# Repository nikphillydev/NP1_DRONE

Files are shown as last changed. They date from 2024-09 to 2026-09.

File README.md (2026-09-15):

# NP1 DRONE
I am attempting to build a quadcopter from scratch, both the PCB hardware (using KiCAD) and software (C/C++ on STM32).

I am a computer software engineering student at the University of Alberta. I started this project in early 2024 to push myself with embedded systems. Since its inception, I have learned a ton about PCB design and FreeRTOS firmware on STM32 microcontrollers. 

Everything I make in this project is from scratch. The STM32-based circuit boards are designed with KiCAD and ordered from JLCPCB with assembly. I am using FreeRTOS for the software because of its scalability in complex embedded projects. I have written all the device drivers from scratch, and wholly designed the multi-threaded architecture for each of the drone's sub-systems.

Each sub-system presents its own set of challenges. As an overview, there are 3 sub-systems of the NP1 Drone:
```
                     (Over-The-Air Messaging)                               (CANBUS)
[RC CONTROLLER]   <---------------------------->  [Flight Controller]   <--------------->  [Electronic Speed Controller] x4
```
#### 1. Flight Controller Overview
The Flight Controller (FCC) is a custom PCB design whose software runs the control system for the drone. In order to achieve this, it must 1) receive pilot input from the RC Controller, and 2) estimate its attitude and heading (roll, pitch, yaw). These inputs enter the onboard PID controller in order to calculate the necessary motor commands to send to the Electronic Speed Controllers (ESCs).

The FCC is equipped with a multitude of sensors, namely an IMU, magnetometer, barometer, optical flow sensor, and range finder. It performs sensor fusion through the use of an Extended Kalman Filter (EKF) and a few other custom algorithms. When it receives Over-The-Air (OTA) messages from the RC Controller, it monitors for a HEARTBEAT signal to detect LOSS-OF-LINK and perform flight termination. The control system interprets pilot input and sets the target roll, pitch, and yaw accordingly depending on flight mode (various flight modes still WIP).

<p align="center">
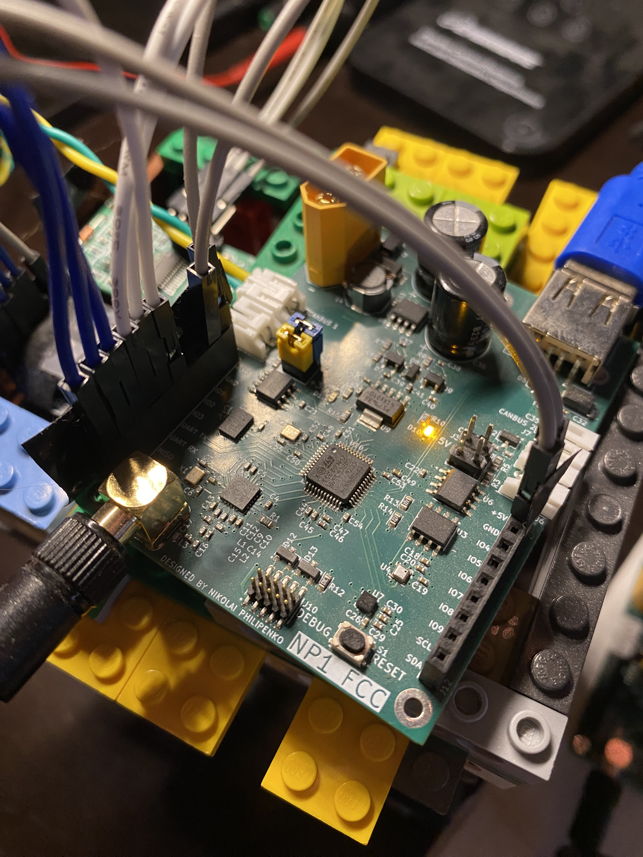
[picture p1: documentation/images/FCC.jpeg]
Flight Controller
  <br>
  <sub><b>Figure 1:</b> The Flight Controller (FCC) sitting on a Lego frame. The USB powers the board and enables logging to my laptop; jumper wires connect the external range finder and optical flow sensor; the green and yellow twisted pair connect to the ESCs using CANBUS.</sub>
</p>

#### 2. RC Controller Overview
The RC Controller is simple: receive pilot input from various joysticks and buttons and send those values Over-The-Air (OTA) to the FCC. A custom OTA messaging protocol (modelled after MAVLINK) has been developed to facilitate this communication. The physical inputs of the RC Controller are fairly WIP right now. Currently, its a breadboard with push-buttons and a potentiometer, (hopefully) soon it will be a PS4 controller.

<p align="center">
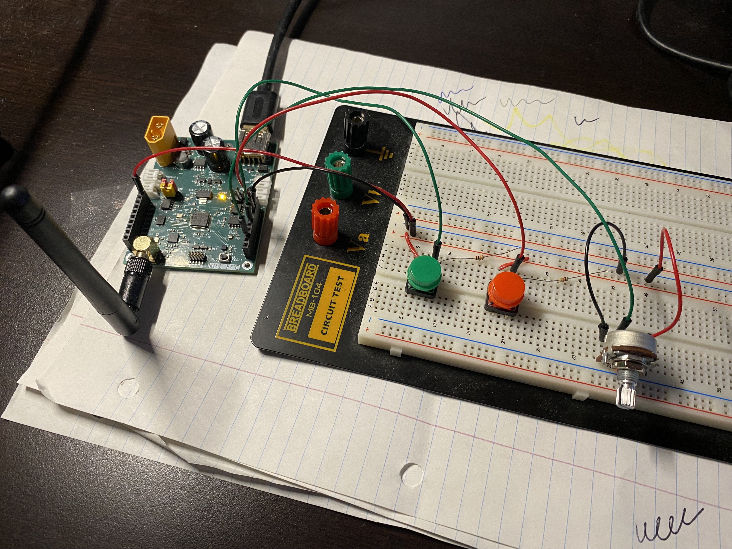
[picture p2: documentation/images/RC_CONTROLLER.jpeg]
RC Controller
  <br>
  <sub><b>Figure 2:</b> The RC Controller, in its current state. Spare hardware is used to capture pilot input.</sub>
</p>

#### 3. Electronic Speed Controller Overview
The Electronic Speed Controller (ESC) requires a strong understanding of Brushless DC (BLDC) motor control. The custom PCB design and software are designed around the (sensorless) 6-Step Trapezoidal control method, where a Back Electromotive Force (BEMF) measurement from the floating motor phase is measured in order to know when to switch the commutation to the next step. In order to perform proper closed-loop control in this method, the motor must be spinning fast enough to generate a sufficient BEMF. I designed the ESC to operate in a software defined state-machine. Here are the states:
1. STAND-BY: ESC is not commanding a rotation of the motor.
2. ARMING: Align-and-Go Step. ESC commands an open-loop ramp up of the motor to obtain sufficient BEMF measurements. Lasts for about 0.8 sec.
3. ARMED: ESC is commanding true closed-loop, 6-Step commutation with BEMF zero-crossing detection.

The ESC receives ARM, DISARM, and THROTTLE CANBUS messages from the FCC to transition between its internal states and increase / decrease motor RPM.

<table align="center">
  <tr>
    <td align="center" valign="top">
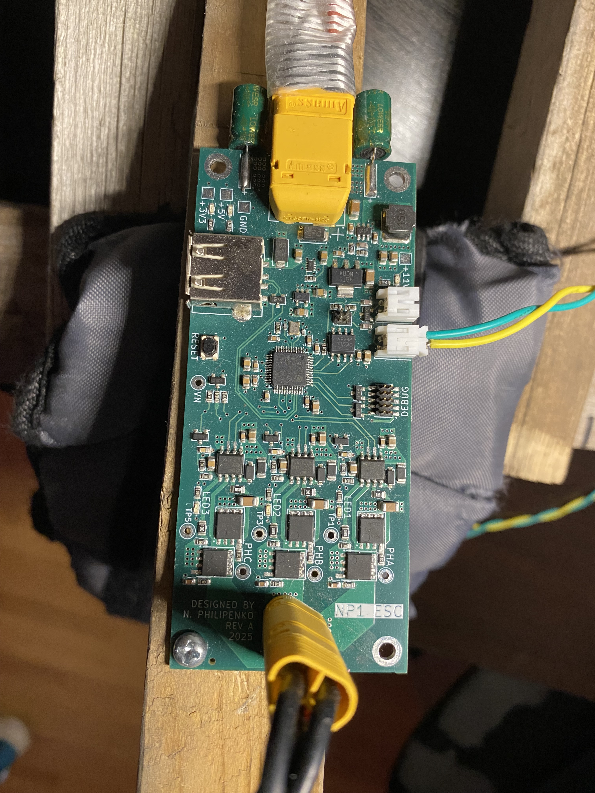
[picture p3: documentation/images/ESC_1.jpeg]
Electronic Speed Controller
      <br>
      <sub><b>Figure 2:</b> The Electronic Speed Controller (ESC), connected to the FCC via CANBUS.</sub>
    </td>
    <td align="center" valign="top">
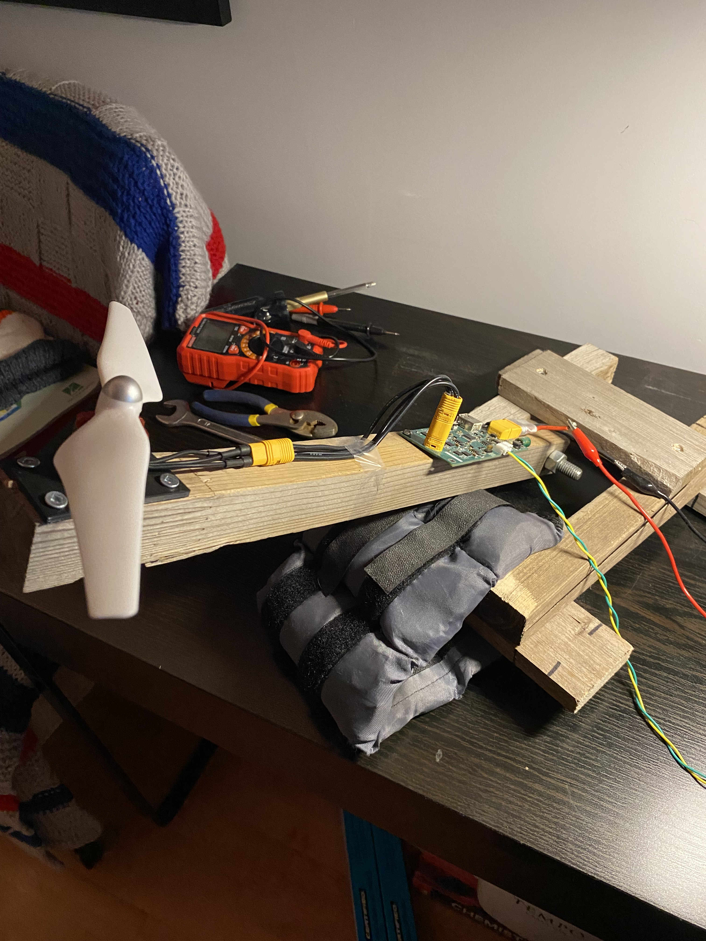
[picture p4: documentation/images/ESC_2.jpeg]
Motor Test Stand
      <br>
      <sub><b>Figure 3:</b> The motor test stand; an ESC and BLDC motor mounted onto a wooden lever.</sub>
    </td>
  </tr>
</table>

### System Demo
This demo showcases the RC Controller sending my input Over-The-Air (OTA) to the FCC. The FCC receives these commands and uses its estimated state to calculate motor commands in its control system. The resulting commands are sent via CANBUS to the ESC on the motor test stand, controlling the BLDC motor.

https://github.com/user-attachments/assets/3e73fd2b-c005-44b4-9096-01581734d467

### In-Depth Design
For more detailed design, please see the hardware and software folders.

Here is the [hardware overview](hardware/README.md).

Here is the [software overview](software/STM32/README.md).

### A Note on the Use of AI
When I started the project in 2024, zero AI was used. Now, from 2026 onward, AI is obviously much better. However, this is a PASSION PROJECT. The goal of this project is to LEARN. I will not be able to effectively achieve that goal if I use AI. The intelligence you gain from AI is artificial. Therefore, I write all the code MYSELF. If there are bugs or I want some review / feedback of my work, I will use AI to do so. In this way, AI is the reviewer and I formulate my own thoughts first.

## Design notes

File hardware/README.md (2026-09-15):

## Hardware Overview
This project includes 2 custom PCB designs: 
1. Flight Control Computer (FCC)
2. Electronic Speed Controller (ESC)

#### PCB: Flight Control Computer [COMPLETE]
The FCC PCB incorporates:
- STM32G474 microcontroller
- BMI088 IMU (accelerometer + gyroscope), LIS3MDL magnetometer, BMP388 barometer
- USB 2.0 Full Speed (Data + Power)
- 2 SN65HVD232 CANbus transceivers (one bus for ESC comms and another bus for serial payloads)
- CC2500 2.4GHz RF transceiver (for comms with ground station)
- M24C32 32kBit EEPROM
- Power regulation (4S / 6S LIPO -> +5V -> +3.3V)
- Payload header (exposing +5V, +3.3V, GPIO, I2C, SPI, UART)

#### PCB: Electronic Speed Controller [COMPLETE]
The ESC PCB incorporates:
- STM32G474 microcontroller
- 3 Half-bridge MOSFET gate drivers to support a 3 phase BLDC motor
- 6 N-channel power MOSFETS (in 3 half-bridge topologies)
- Per phase voltage measurement
- Back-EMF zero-crossing detection (using MCU comparators)
- CANbus transceiver (comms to FCC)
- Power regulation (4S / 6S LIPO -> +11V -> +5V -> +3.3V)

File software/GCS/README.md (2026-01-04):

## NP1 Ground Control Station

The NP1 GCS software is a PyQT6 application that reads from a USB serial port that the NP1 FCC is sending vehicle data to. This data is formatted in such a way that the GCS software can parse and display the data into a GUI for visualization. The displayed information includes vehicle state data (XY velocity, current orientation, and altitude) and general logging information.

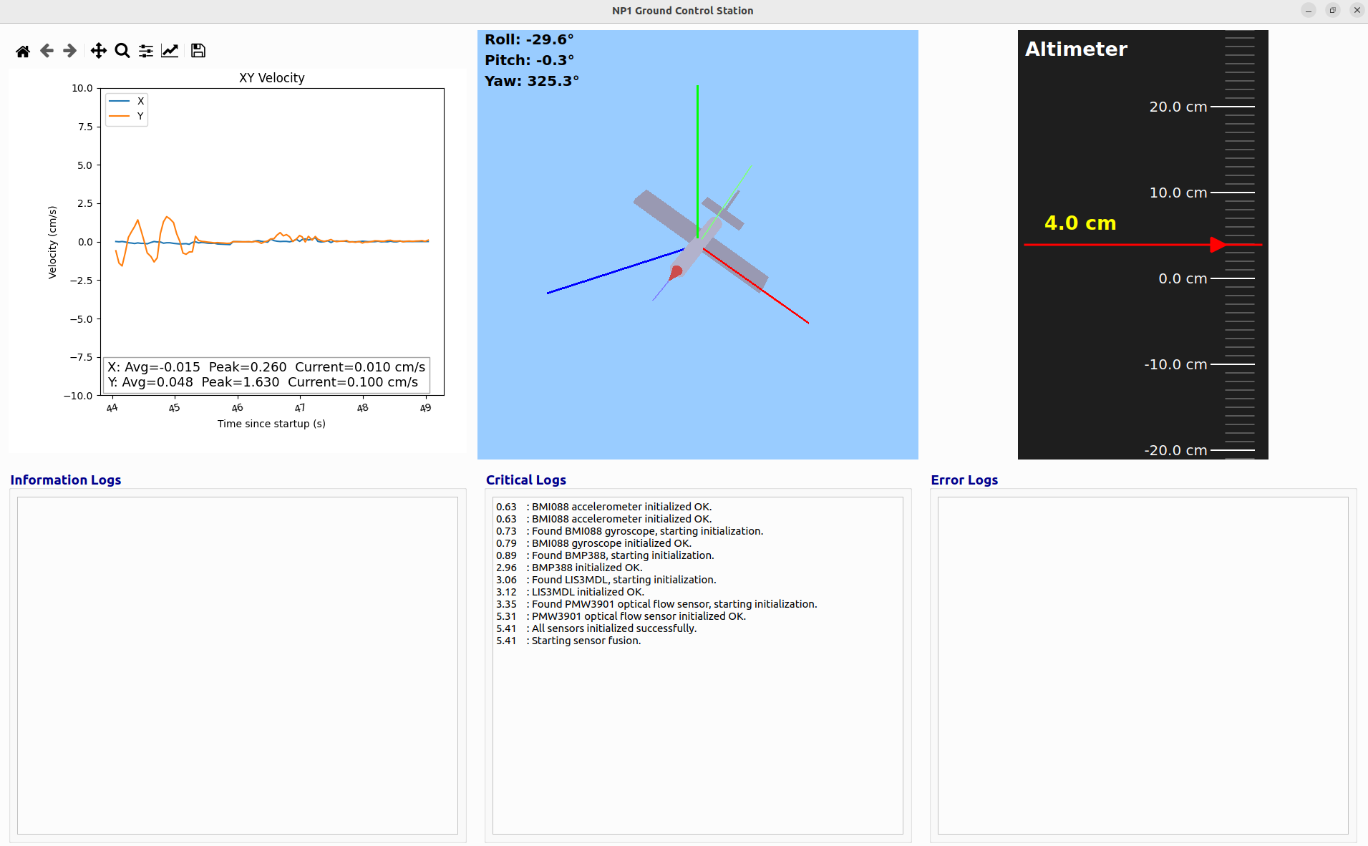
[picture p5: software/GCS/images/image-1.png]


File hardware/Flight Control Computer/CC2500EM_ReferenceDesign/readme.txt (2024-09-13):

XXXXXXXXXXXXXXXXXXXXXXXXXXXXXXXXXXXXXXXXXXXXXXXXXXXXXXXXXXXXXXXXXXXXXXXXXXXXXXXXX
X   Artwork and documentation done by: Texas Instruments Norway AS              X
X   Company: Texas Instruments Norway AS                                        X
X   Address: Gaustadalléen 21    0349 OSLO                                      X
X                                                                               X
X                                                                               X
XXXXXXXXXXXXXXXXXXXXXXXXXXXXXXXXXXXXXXXXXXXXXXXXXXXXXXXXXXXXXXXXXXXXXXXXXXXXXXXXX

PCB NAME : CC2500EM
REVISION: 3.0
DATE: 2010-04-08

Manufacturers marking: Two letter + year + week
The two letter code shall identify the manufaturer and is decided by the manufacturer. 
No logos or other identifiers are allowed.
The marking shall be in silk screen print at secondary side of the PCB, or in solder 
resist if no silk print at secondary side.

FILE: CC2500EM_Reference_Design_3_0.zip PACKED WITH WinZIP 

PCB DESCRIPTION: 2 LAYER PCB 0.8 MM NOMINAL THICKNESS FR4 WITH 35um Cu PER LAYER
        Dielectric constant for FR4 is 4.5
        Dimensions in manufacturing files are in mils (0.001 inch)
                DOUBLE SIDE SOLDER MASK,
                DOUBLE SIDE SILKSCREEN,
                8 MIL MIN TRACE WIDTH AND 8 MIL MIN ISOLATION

FILE NAME                   DESCRIPTION                                 FILE TYPE
-------------------------------------------------------------------------------------------
***PCB MANUFACTURING FILES:
L1.SPL                      LAYER 1 COMPONENT SIDE/POSITIV              EXT. GERBER
L2.SPL                      LAYER 2 SOLDER SIDE/POSITIV                 EXT. GERBER
STOPCOMP.SPL                SOLDER MASK COMPONENT SIDE/NEGATIVE         EXT. GERBER
STOPSOLD.SPL                SOLDER MASK SOLDER SIDE/NEGATIVE            EXT. GERBER
SILKCOMP.SPL                SILKSCREEN COMPONENT SIDE/POSITIVE          EXT. GERBER
SILKSOLD.SPL                SILKSCREEN SOLDER SIDE/POSITIVE             EXT. GERBER
NCDRILL.SPL                 NC DRILL THROUGH HOLE                       EXCELLON
DRILL.SPL                   DRILL/MECHANICAL DRAWING                    EXT. GERBER
GERBER.REP                  DRILL and NC DRILL REPORT                   ASCII
EXT_GERBER.USR              EXTENDED GERBER APERTURE TABLE              ASCII
CNC.USR                     NC DRILL DEVICE FILE                        ASCII

***PCB ASSEMBLY FILES:
CC2500EM_PARTLIST_3_0.XLS   PART LIST                                   ASCII
P&P_COMP.REP                PICK AND PLACE COORDINATES, COMPONENT SIDE  ASCII
P&P_SOLD.REP                PICK AND PLACE COORDINATES, SOLDER SIDE     ASCII
PASTCOMP.SPL                SOLDER PASTE COMPONENT SIDE                 EXT. GERBER
PASTSOLD.SPL                SOLDER PASTE SOLDER SIDE                    EXT. GERBER
ASSYCOMP.SPL                ASSEMBLY DRAWING COMPONENT SIDE             EXT. GERBER
ASSYSOLD.SPL                ASSEMBLY DRAWING SOLDER SIDE                EXT. GERBER

***PDF FILES:
CC2500EM_SCHEMATIC_3_0.PDF  SCHEMATIC FILE                              PDF
CC2500EM_LAYOUT_3_0.PDF     ASSEMBLY DRAWING                            PDF
      
***CADSTAR FILES:
CC2500EM_3_0.SCM            Cadstar Schematic file
CC2500EM_3_0.PCB            Cadstar layout file

***OTHER FILES:
README.TXT                  THIS FILE     

END.

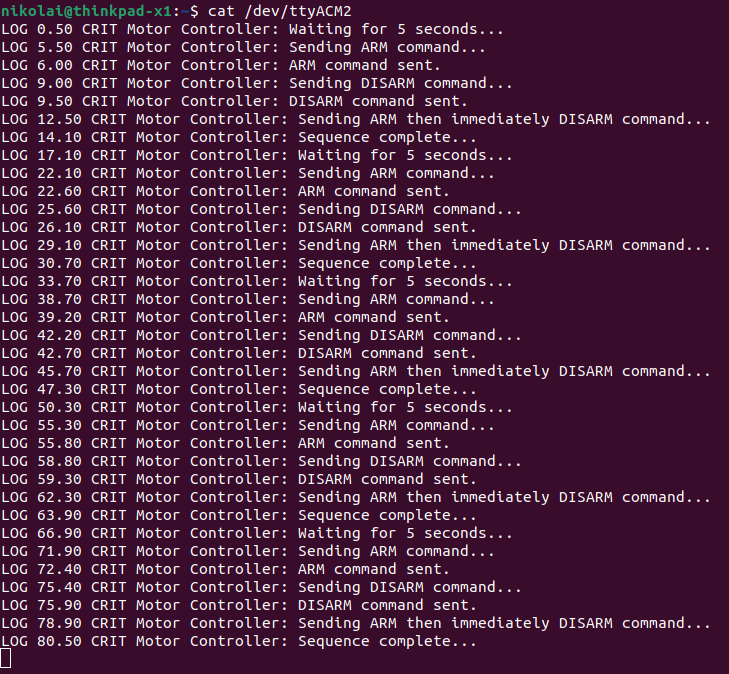
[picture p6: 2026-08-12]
documentation/report/Screenshot from 2026-06-04 21-25-31.png

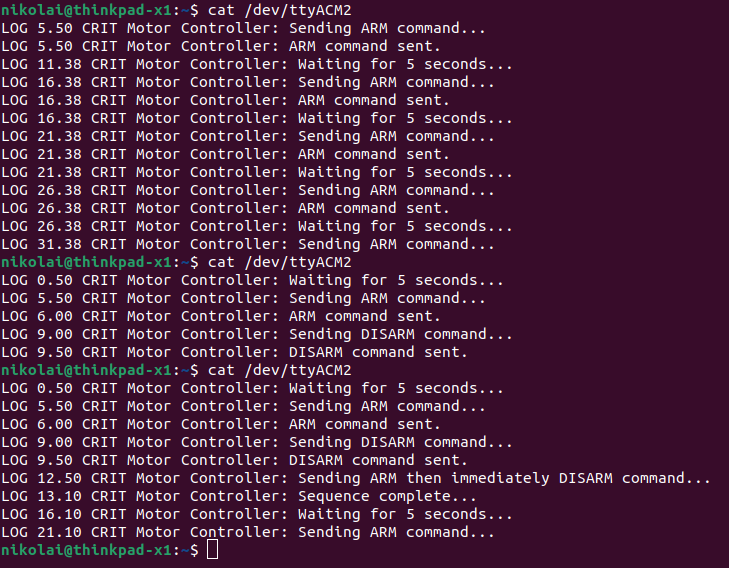
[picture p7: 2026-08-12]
documentation/report/Screenshot from 2026-06-04 21-16-27.png

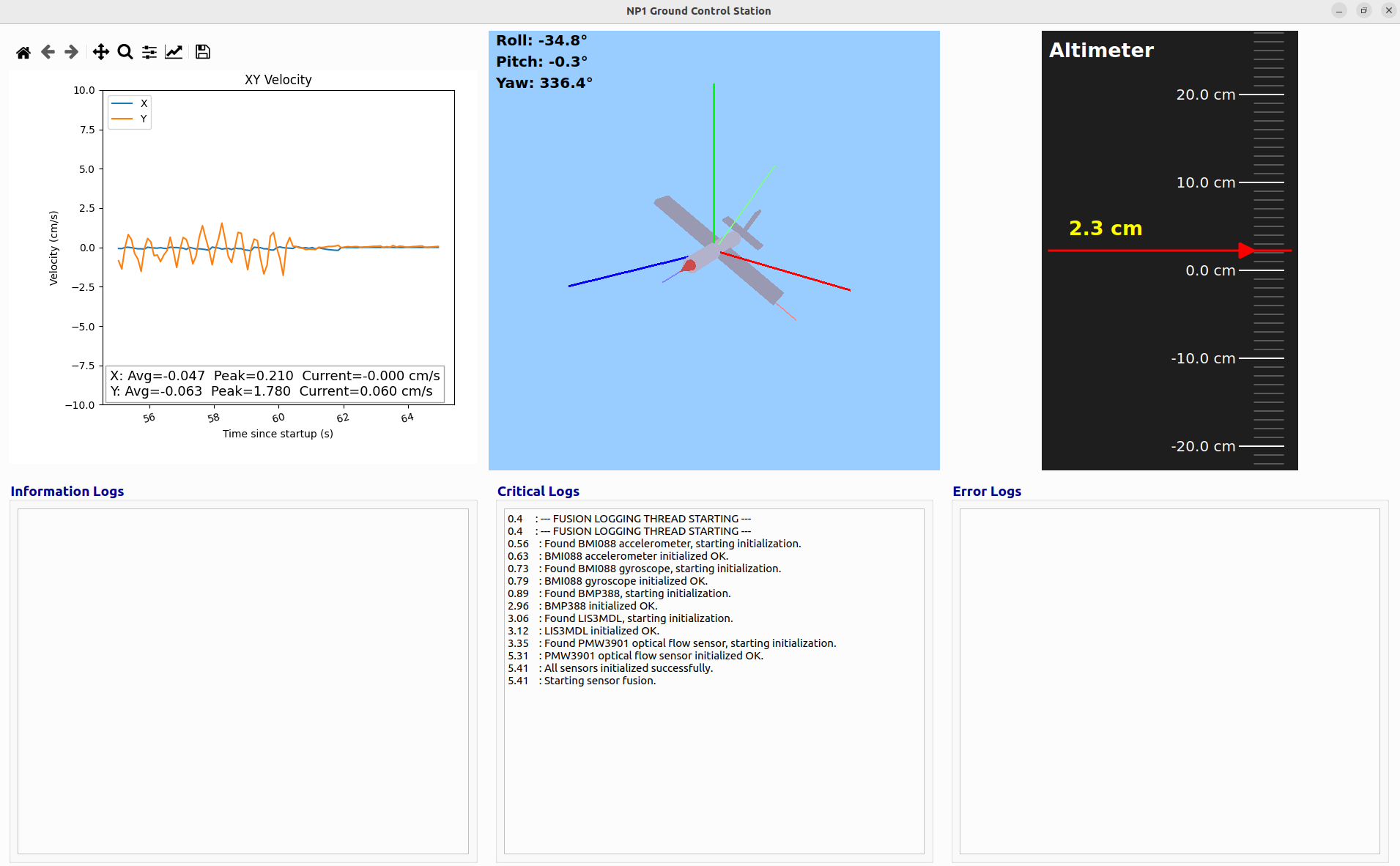
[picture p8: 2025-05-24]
software/GCS/images/image.png

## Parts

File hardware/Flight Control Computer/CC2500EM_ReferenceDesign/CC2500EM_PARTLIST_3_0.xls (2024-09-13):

CC2500EM Parts list
This list is automatically linked up to the G:\06_TEKNISK\06H_Cadstar\purchase_library\PurchaseLib.xls
Enter columns in green
Ref. | Part name | Pcs/unit | Description | Manufacturer | Part number | Supplier | Ordering code | Alt. Manufacturer | Alt. Part number | Alt. Supplier | Alt. Ordering code | Comments
U1 | CC2500 | 1 | Single-chip transceiver | TI | CC2500 | TI | CC2500 |  |  |  |  | Supplied by Chipcon
C41;C51;C111;C141 | C_100N_0402_X5R_K_10 | 4 | Capacitor, 100n, 0402, X5R, 10%, 10V | Murata | GRM155R71A104KA01D
C121;C131 | C_100P_0402_NP0_J_50 | 2 | Capacitor, 100p, 0402, NP0, 5% 50V | Murata | GRM1555C1H101JZ01D
C81;C101 | C_10P_0402_NP0_J_50 | 2 | Capacitor, 10p, 0402, NP0, 5%, 50V | Murata | GRM1555C1H100JZ01D
C122;C132 | C_1P0_0402_NP0_C_50 | 2 | Capacitor, 1p, 0402, NP0, +/-0.25pF 50V | Murata | GRM1555C1H1R0CZ01D
C124 | C_1P5_0402_NP0_C_50 | 1 | Capacitor, 1p5, 0402, NP0, +-0.25pF, 50V | Murata | GRM1555C1H1R5CZ01D
C123 | C_1P8_0402_NP0_C_50 | 1 | Capacitor, 1p8, 0402, NP0, +/-0.25pF 50V | Murata | GRM1555C1H1R8CZ01D
C1 | C_1U_0805_X7R_K_16 | 1 | Capacitor, 1u, 0805, X7R, 10%, 16V | Murata | GRM21BR71C105KA01L | ELFA | 65-809-71
C91;C151;C181 | C_220P_0402_X7R_K_50 | 3 | Capacitor, 220p, 0402, X7R, 10%, 50V | Murata | GRM155R71H221KA01D
FM1-3 | FIDUCIAL_MARK | 3 | #N/A | #N/A | #N/A | #N/A | #N/A | #N/A | #N/A | #N/A | #N/A | #N/A
L121-122;L131 | L_1N2_0402_S | 3 | Inductor, 1n2, 0402, Monolithic type, +/-0.3 nH | Murata | LQG15HS1N2S02D | ACTE |  | Coilcraft
L1 | L_BEAD_102_0402 | 1 | EMI filter bead, 0402 1Kohms Tape GHz Band Gen Use | Murata | BLM15HG102SN1D | ACTE
R171 | R_56K_0402_F | 1 | Resistor, 56k ohms, 0402, ±1% | Koa | RK73H1ETTP5602F | ELFA | 60-488-96
P3 | SMA_SMD | 1 | SMA connector, straight SMD-mount | Hus-Tsan Group Taiwan | SMA-10V21-TGG | EC Partner A/S | SMA-10V21-TGG |  |  | AFU, Arrow
P1-2 | SMD_SOCKET_2x10 | 2 | SMD pinrow socket, .050 spacing, 2x10 | Samtec | SFM-110-02-SM-D-A-K-TR | Abacus |  |  |  | AFU, Arrow
X1 | X_26.000/10/10/40/10 | 1 | Crystal, 26MHz, 10pF, 10PPM, 2x1.6mm SMD, FA128, 60 ohms | Epson Toyocom | FA128, 26MHZ, 10PPM, 10PF (9PF) | Farnell | 1712808
Total no of components |  | 29
New XTAL being used
Epson Toyocom FA128 26 MHz 2x1.6mm 10pF

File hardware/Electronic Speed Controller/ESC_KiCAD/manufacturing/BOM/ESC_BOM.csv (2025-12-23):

Reference | Value | Description | Qty | JLCPCB Part # | Manufacturer | Manufacturer Part #
C1,C8,C11,C17,C43 | 4.7uF | CAP CER 4.7UF 25V X5R 0805 | 5 | C1779 | Samsung Electro-Mechanics | CL21A475KAQNNNE
C2,C9,C12,C18,C27,C28,C31,C39,C42,C44,C45,C47,C49 | 100nF | CAP CER 0.1UF 50V X7R 0603 | 13 | C14663 | YAGEO | CC0603KRX7R9BB104
C3,C13,C19,C29,C30,C33,C36,C38,C40 | 1uF | CAP CER 1UF 50V X7R 0805 | 9 | C28323 | Samsung Electro-Mechanics | CL21B105KBFNNNE
C4,C5 | 47pF | CAP CER 47PF 50V C0G/NP0 0603 | 2 | C1671 | Samsung Electro-Mechanics | CL10C470JB8NNNC
C6,C14,C20,C23,C26 | 10uF | CAP CER 10UF 50V X5R 1206 | 5 | C13585 | Samsung Electro-Mechanics | CL31A106KBHNNNE
C7,C15,C21 | 1nF | CAP CER 1000PF 50V X7R 0603 | 3 | C1588 | Samsung Electro-Mechanics | CL10B102KB8NNNC
C10,C16,C22,C37,C41 | 10nF | CAP CER 10000PF 50V X7R 0603 | 5 | C57112 | Samsung Electro-Mechanics | CL10B103KB8NNNC
C24,C25 | 330uF | CAP ALUM 330UF 20% 35V RADIAL TH | 2 | C75177 | Rubycon | 35ZLH330MEFC10X12.5
C32 | 100pF | CAP CER 100PF 50V C0G/NP0 0603 | 1 | C14858 | Samsung Electro-Mechanics | CL10C101JB8NNNC
C34,C35 | 22uF | CAP CER 22UF 25V X5R 0805 | 2 | C45783 | Samsung Electro-Mechanics | CL21A226MAYNNNE
C46,C48 | 11pF | CAP CER 11PF 50V C0G/NP0 0402 | 2 | C710643 | Murata Electronics | GCM1555C1H110JA16D
D1,D6,D10 | MBR0580S1-7 | DIODE SCHOTTKY 80V 500MA SOD123 | 3 | C177047 | Diodes Incorporated | MBR0580S1-7
D2,D16,D20,D21 | D1213A-02SOL-7 | TVS DIODE 3.3VWM 10VC SOT233 | 4 | C460585 | Diodes Incorporated | D1213A-02SOL-7
D3,D4,D7,D8,D11,D12 | TPH1R306P1,L1Q | MOSFET N-CH 60V 100A 8SOP | 6 | C6290261 | Toshiba Semiconductor and Storage | TPH1R306P1,L1Q
D5,D9,D13,D22 | BZX84C3V3-7-F | DIODE ZENER 3.3V 300MW SOT23-3 | 4 | C177019 | Diodes Incorporated | BZX84C3V3-7-F
D14,D15 | SMAJ28CA | TVS DIODE 28VWM 45.4VC DO214AC | 2 | C148228 | Littelfuse Inc. | SMAJ28CA
D17,D18,D19,D23,D24,D25 | LED | LED YELLOW CLEAR 0603 SMD | 6 | C72038 | Everlight Electronics Co Ltd | EAST16086YA4
J1,J2 | S2B-PH-K-S | CONN HEADER R/A 2POS 2MM | 2 | C173752 | JST Sales America Inc. | S2B-PH-K-S
J3 | 2x2-1.27MM | CONN HEADER VERT 4POS 1.27MM | 1 | C18197867 | Sullins Connector Solutions | GRPB022VWVN-RC
J4 | XT60PW-M | XT60 HORIZONTAL 2-PIN POWER | 1 | C98732 | Changzhou Amass Elec | XT60PW-M
J5 | USB TYPE-A | CONN RCPT USB2.0 TYPEA 4P SMD RA | 1 | C599118 | Amphenol ICC (FCI) | 87583-2010BLF
J6 | 2x5-1.27MM | CONN HEADER SMD 10POS 1.27MM | 1 | C150517 | Amphenol ICC (FCI) | 20021121-00010C4LF
J7 | MT60-F | MT60 VERT 3-PIN POWER | 1 | C40020701 | Amass Electronics | MT60-F
L1 | 15uH | FIXED IND 15UH 2.05A 88MOHM SMD | 1 | C83374 | Shenzhen Sunlord Electronics Co., Ltd. | SWPA6045S150MT
R1,R11,R19 | 2.2R | RES SMD 2.2 OHM 1% 3/4W 1206 | 3 | C1854860 | Vishay Dale | CRCW12062R20FKEAHP
R2,R3,R12,R13,R20,R21 | 10R/250mW | RES 10 OHM 1% 1/4W 0805 | 6 | C727983 | YAGEO | AC0805FR-7W10RL
R4,R5,R9,R14,R15,R17,R22,R23,R25,R27,R34,R35 | 10k | RES 10K OHM 1% 1/10W 0603 | 12 | C25804 | Stackpole Electronics Inc | RMCF0603FT10K0
R6,R7 | 120R | RES 120 OHM 1% 1/10W 0603 | 2 | C22787 | YAGEO | RC0603FR-07120RL
R8,R16,R24,R37,R38,R39 | 68k | RES SMD 68K OHM 1% 1/10W 0603 | 6 | C23231 | Panasonic Electronic Components | ERJ-3EKF6802V
R10,R18,R26 | 10R | RES 10 OHM 1% 1/10W 0603 | 3 | C22859 | YAGEO | RC0603FR-0710RL
R28 | 100k | RES 100K OHM 1% 1/10W 0603 | 1 | C25803 | YAGEO | RC0603FR-07100KL
R29,R31 | 5.76k | RES 5.76K OHM 1% 1/10W 0603 | 2 | C2933239 | YAGEO | RC0603FR-075K76L
R30 | 4.7k | RES 4.7K OHM 1% 1/10W 0603 | 1 | C23162 | YAGEO | RC0603FR-074K7L
R32 | 3k | RES 3K OHM 1% 1/10W 0603 | 1 | C4211 | Stackpole Electronics Inc | RMCF0603FT3K00
R33,R36,R40,R41 | 1k | RES 1K OHM 1% 1/10W 0603 | 4 | C21190 | Stackpole Electronics Inc | RMCF0603FT1K00
S1 | SKRPARE010 | TACT SWITCHTTM | 1 | C341730 | Alps Alpine | SKRPARE010
TH1 | NTC 10k | THERMISTOR NTC 10KOHM 3380K 0603 | 1 | C440252 | Murata Electronics | NCU18XH103F60RB
U1,U3,U4 | IRS21867STRPBF | IC GATE DRVR HALF-BRIDGE 8SOIC | 3 | C52290 | Infineon Technologies | IRS21867STRPBF
U2 | SN65HVD232DR | IC TRANSCEIVER HALF 1/1 8SOIC | 1 | C30530 | Texas Instruments | SN65HVD232DR
U5 | LM7805MPX/NOPB | IC REG LINEAR 5V 1.5A SOT-223-4 | 1 | C2848241 | Texas Instruments | LM7805MPX/NOPB
U6 | TPS54302DDCR | IC REG BUCK ADJ 3A SOT23 | 1 | C311983 | Texas Instruments | TPS54302DDCR
U7 | LM66200DRLR | IC POWER OR CONTROLLER | 1 | C3235556 | Texas Instruments | LM66200DRLR
U8 | TLV75533PDBVR | IC REG LINEAR 3.3V 500MA SOT23-5 | 1 | C404027 | Texas Instruments | TLV75533PDBVR
U9 | STM32G474CET6 | IC MCU 32BIT 512KB FLASH 48LQFP | 1 | C730125 | STMicroelectronics | STM32G474CET6
X1 | NX2520SA-16MHz | CRYSTAL 16.0000MHZ 8PF SMD | 1 | C280836 | NDK (NIHON DEMPA KOGYO CO., LTD) | STDCSW5-16M

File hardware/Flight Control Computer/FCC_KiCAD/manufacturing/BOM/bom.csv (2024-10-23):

Comment | Designator | Footprint | JLCPCB Part # | Manufacturer | Manufacturer Part #
100nF | C1,C2,C5,C7,C9,C13,C18,C19,C20,C21,C22,C25,C26,C30,C34,C45,C48,C50,C51,C53,C54 | Capacitors:CAP_0402_1005Metric | C77020 | Murata Electronics | GRM155R71H104KE14D
11pF | C3,C6,C52,C55 | Capacitors:CAP_0402_1005Metric | C710643 | Murata Electronics | GCM1555C1H110JA16D
220pF | C4,C8,C10 | Capacitors:CAP_0402_1005Metric | C97872 | Murata Electronics | GRM155R71H221KA01D
100pF | C11,C12 | Capacitors:CAP_0402_1005Metric | C77177 | Murata Electronics | GRM1555C1H101JA01D
1pF | C14,C15 | Capacitors:CAP_0402_1005Metric | C76953 | Murata Electronics | GRM1555C1H1R0CA01D
1.8pF | C16 | Capacitors:CAP_0402_1005Metric | C85878 | Murata Electronics | GJM1555C1H1R8CB01D
1.5pF | C17 | Capacitors:CAP_0402_1005Metric | C76958 | Murata Electronics | GRM1555C1H1R5CA01D
47pF | C23,C24,C27,C28 | Capacitors:CAP_0402_1005Metric | C76970 | Murata Electronics | GRM1555C1H470JA01D
1uF | C29,C37,C38,C39,C40,C43,C44,C46 | Capacitors:CAP_0402_1005Metric | C77009 | Murata Electronics | GRM155R61E105KA12D
150uF | C31,C36 | Capacitors:NICHICON_UHE_10x12.5 | C116230 | Nichicon | UHE1H151MPD
10nF | C32,C33,C42,C47 | Capacitors:CAP_0402_1005Metric | C162190 | Murata Electronics | GRM155R71H103JA88D
6.8uF | C35 | Capacitors:CAP_0603_1608Metric | C338096 | TDK Corporation | C1608X5R1A685K080AC
2.2uF | C41 | Capacitors:CAP_0402_1005Metric | C385032 | Murata Electronics | GRM155R61E225KE11D
4.7uF | C49 | Capacitors:CAP_0402_1005Metric | C77004 | Murata Electronics | GRM155R61A475KEAAD
D1213A-02SOL | D1,D2,D5,D12,D13 | Diodes:DiodesINC_SOT23-3 | C460585 | Diodes Incorporated | D1213A-02SOL-7
SMAJ45A | D3 | Diodes:DiodesINC_SMA | C134989 | Diodes Incorporated | SMAJ45A-13-F
SMAJ5.0A | D4 | Diodes:DiodesINC_SMA | C87074 | Diodes Incorporated | SMAJ5.0A-13-F
B150 | D6 | Diodes:DiodesINC_SMA | C134431 | Diodes Incorporated | B150-13-F
MAX40200AUK | D7,D9 | Diodes:AnalogDevices_SOT23-5 | C2649430 | Analog Devices Inc./Maxim Integrated | MAX40200AUK+T
DMN65D8L | D8 | Diodes:DiodesINC_SOT23-3 | C155341 | Diodes Incorporated | DMN65D8L-7
LED | D10,D11 | Diodes:LED_0603_1608Metric | C72038 | Everlight Electronics Co Ltd | 19-213/Y2C-CQ2R2L/3T
330R | FB1 | Inductors:L_0603_1608Metric | C710391 | Murata Electronics | BLM18SG331TZ1D
50 Ohm | J1 | Connectors:RF-SMA_Dosinconn_DOSIN-806-0001 | C521220 | Dosin Electronics | DOSIN-806-0001
2x2-2.54MM | J2,J3 | Connectors:CONN_MALE_TH_2.54MM_2x2 | C66690 | BOOMELE(Boom Precision Elec) | 2.54-2*2P
S2B-PH-K-S | J4,J5,J6,J7 | Connectors:CONN_JST_S2B-PH-K-S | C173752 | JST Sales America Inc. | S2B-PH-K-S
XT60 | J8 | Connectors:CONN_MALE_TH_XT60 | C98733 | Changzhou Amass Elec | XT60
USB TYPE-A | J9 | Connectors:USB2.0_4P_AMPHENOL_87583-2010BLF | C599118 | Amphenol ICC (FCI) | 87583-2010BLF
2x5-1.27MM | J10 | Connectors:CONN_MALE_SMT_1.27MM_2x5 | C150517 | Amphenol ICC (FCI) | 20021121-00010C4LF
1x10-2.54MM | J11,J12 | Connectors:CONN_FEMALE_TH_2.54MM_1x10 | C2897373 | HCTL | PM254-1-10-Z-8.5
1.2nH | L1,L2,L3 | Inductors:L_0402_1005Metric | C77105 | Murata Electronics | LQG15HS1N2S02D
47uH | L4 | Inductors:TDK_CLF7045-D | C432960 | TDK Corporation | CLF7045T-470M-D
56k | R1 | Resistors:RES_0603_1608Metric | C144110 | YAGEO | AF0603FR-0756KL
120R | R2,R3,R4,R5 | Resistors:RES_0603_1608Metric | C22787 | UNI-ROYAL(Uniroyal Elec) | 0603WAF1200T5E
0R5 | R6,R11 | Resistors:RES_0603_1608Metric | C309622 | YAGEO | RL0603FR-070R5L
10k | R7,R9,R12,R15 | Resistors:RES_0603_1608Metric | C98220 | YAGEO | RC0603FR-0710KL
100k | R8 | Resistors:RES_0603_1608Metric | C14675 | YAGEO | RC0603FR-07100KL
1k | R10 | Resistors:RES_0603_1608Metric | C22548 | YAGEO | RC0603FR-071KL
2.2k | R13,R14 | Resistors:RES_0603_1608Metric | C114662 | YAGEO | RC0603FR-072K2L
SKRPARE010 | S1 | Switches:TACT_SKRP | C341730 | ALPSALPINE | SKRPARE010
BMI088 | U1 | ICs:BOSCH_LGA-16 | C194919 | Bosch Sensortec | BMI088
CC2500 | U2 | ICs:TI_QFN-20 | C57494 | Texas Instruments | CC2500RGPR
M24C32 | U3 | ICs:STM_SO8N | C79920 | STMicroelectronics | M24C32-RMN6TP
BMP388 | U4 | ICs:BOSCH_LGA-10 | C779278 | Bosch Sensortec | BMP388
SN65HVD232D | U5,U6 | ICs:TI_SOIC-8 | C30530 | Texas Instruments | SN65HVD232DR
LIS3MDL | U7 | ICs:STM_LGA-12L | C478483 | STMicroelectronics | LIS3MDLTR
LM2672 | U8 | ICs:TI_SOIC-8 | C180371 | Texas Instruments | LM2672MX-5.0/NOPB
TPS79633 | U9 | ICs:TI_SOT223-6 | C485803 | Texas Instruments | TPS79633DCQR
STM32G474CET6 | U10 | ICs:STM_LQFP48 | C730125 | STMicroelectronics | STM32G474CET6
NX2520SA-26MHz | X1 | CrystalsAndOscillators:NDK_NX2520SA | C910046 | NDK | NX2520SA-26MHZ-STD-CSW-5
NX2520SA-16MHz | X2 | CrystalsAndOscillators:NDK_NX2520SA | C280836 | NDK | NX2520SA-16MHZ-STD-CSW-5

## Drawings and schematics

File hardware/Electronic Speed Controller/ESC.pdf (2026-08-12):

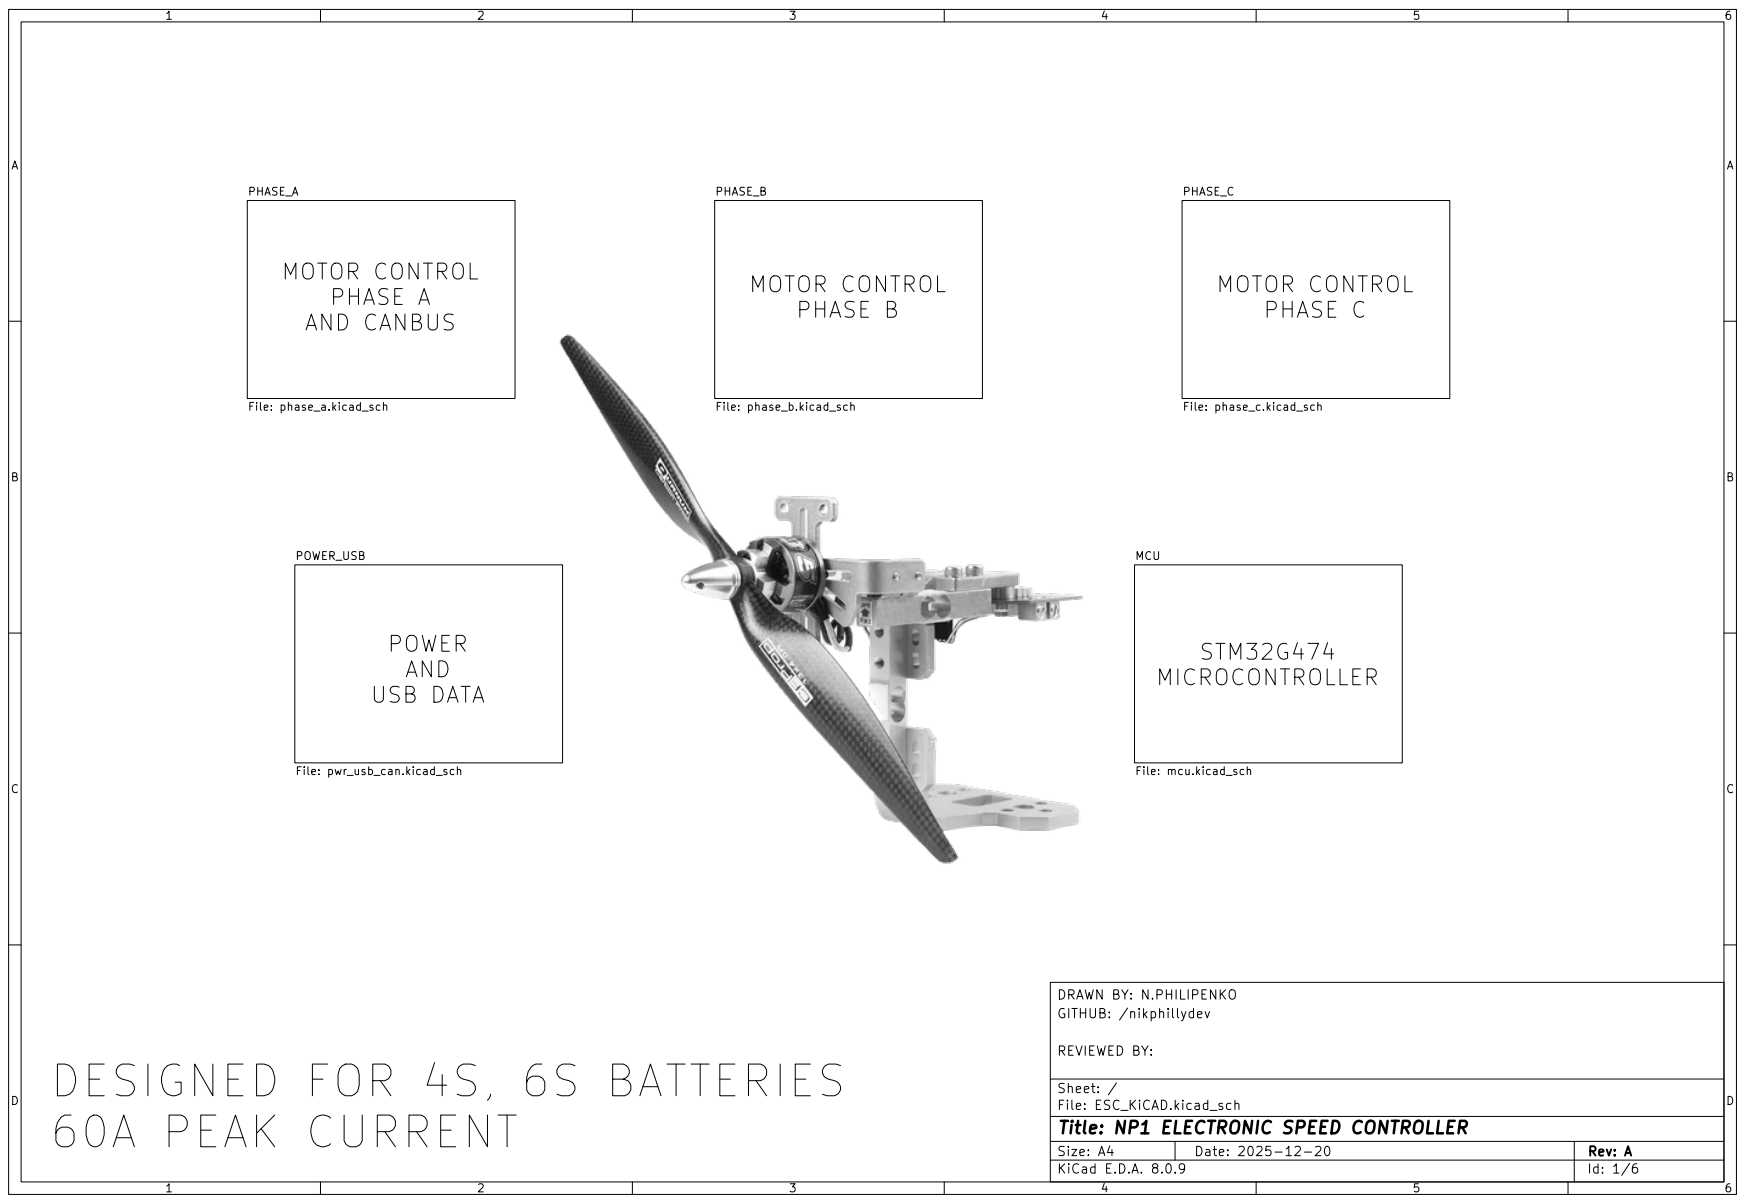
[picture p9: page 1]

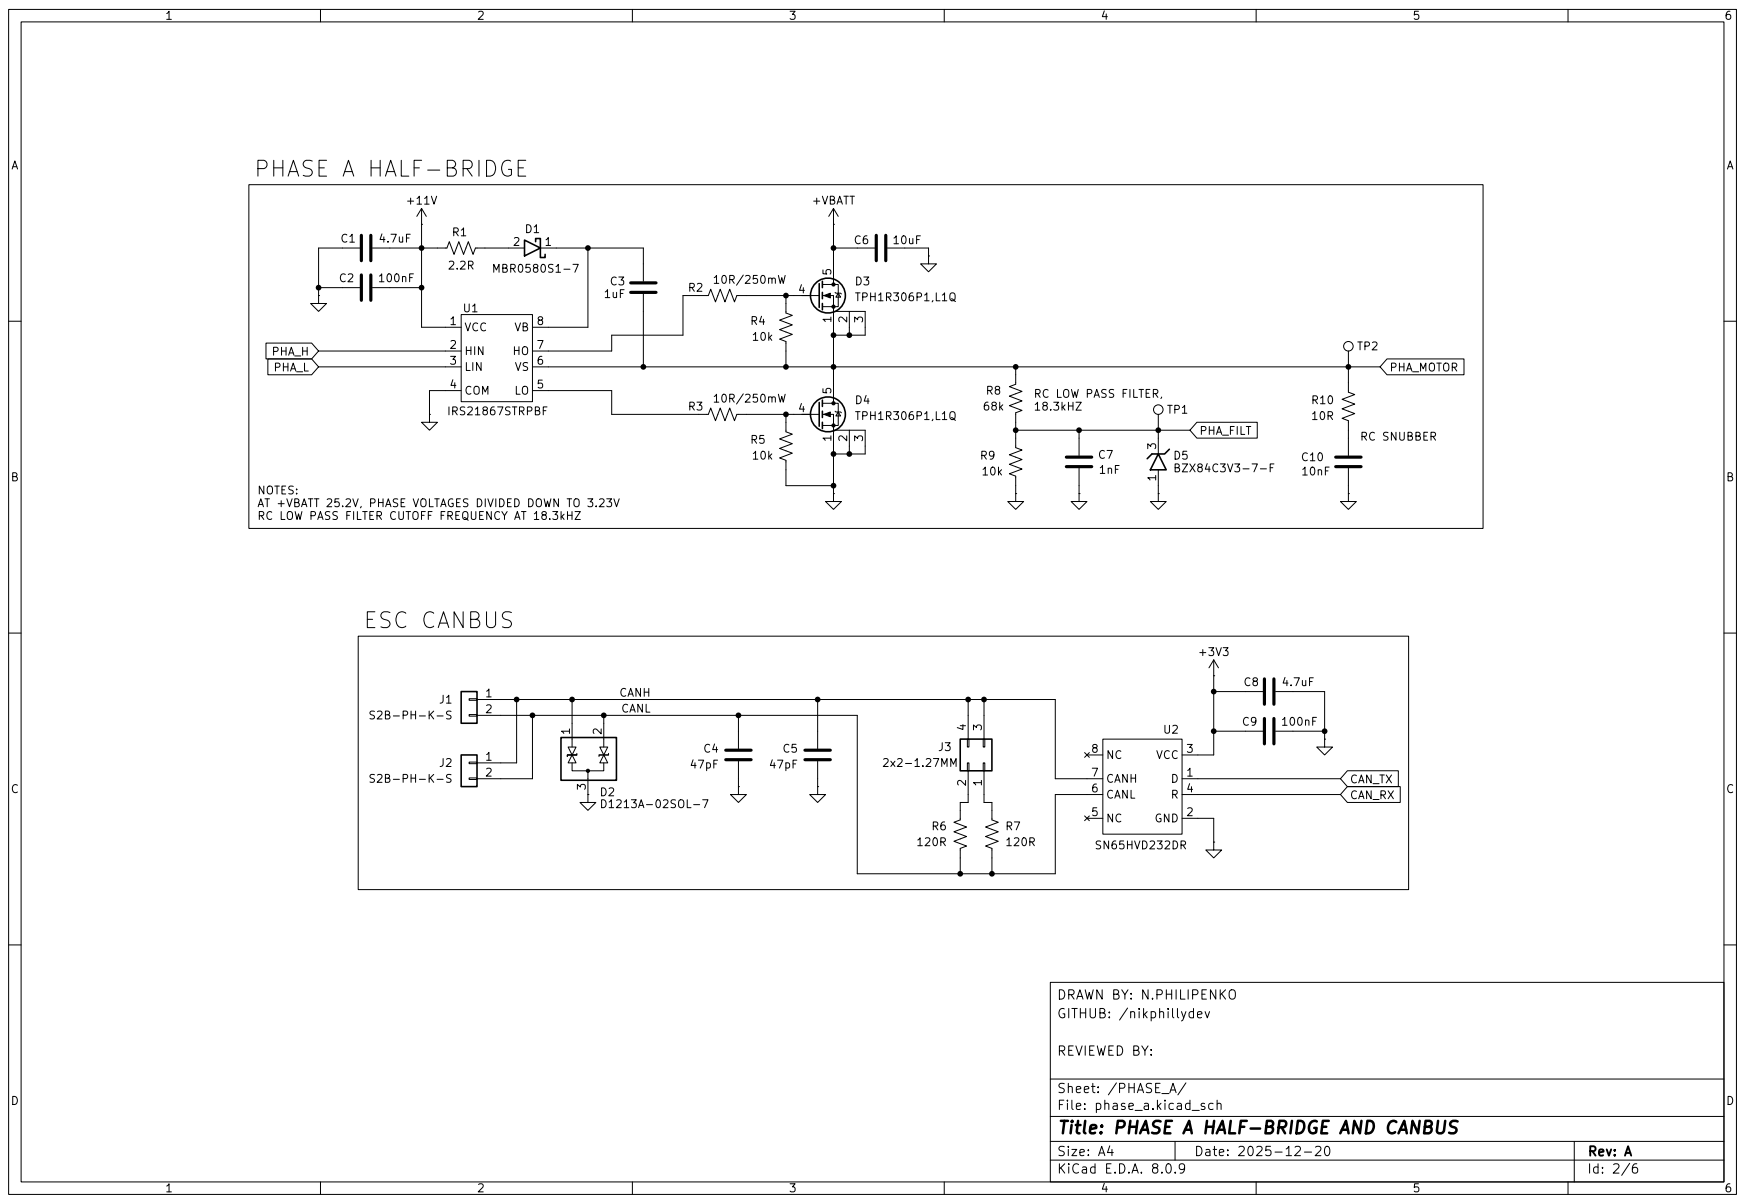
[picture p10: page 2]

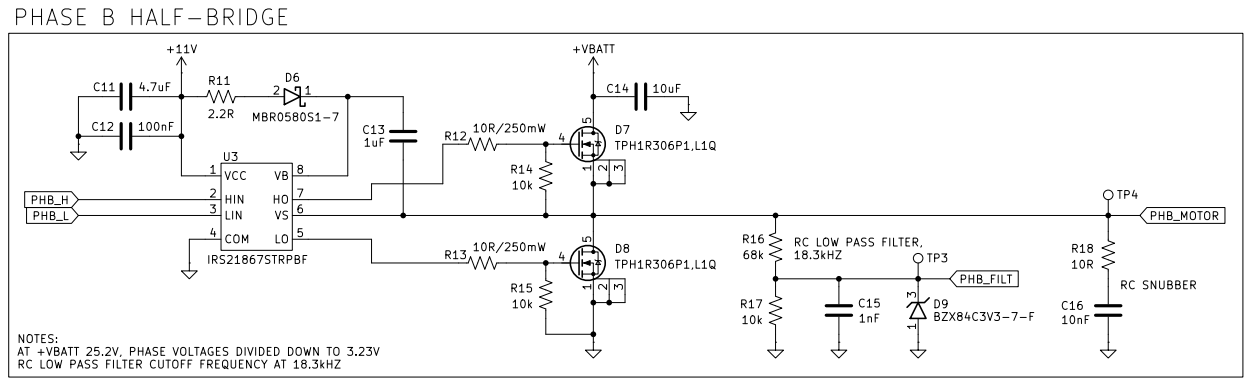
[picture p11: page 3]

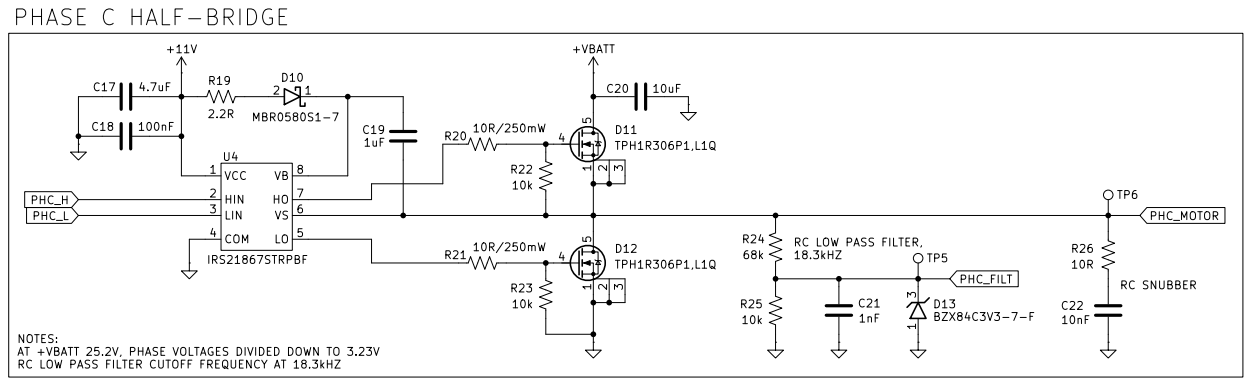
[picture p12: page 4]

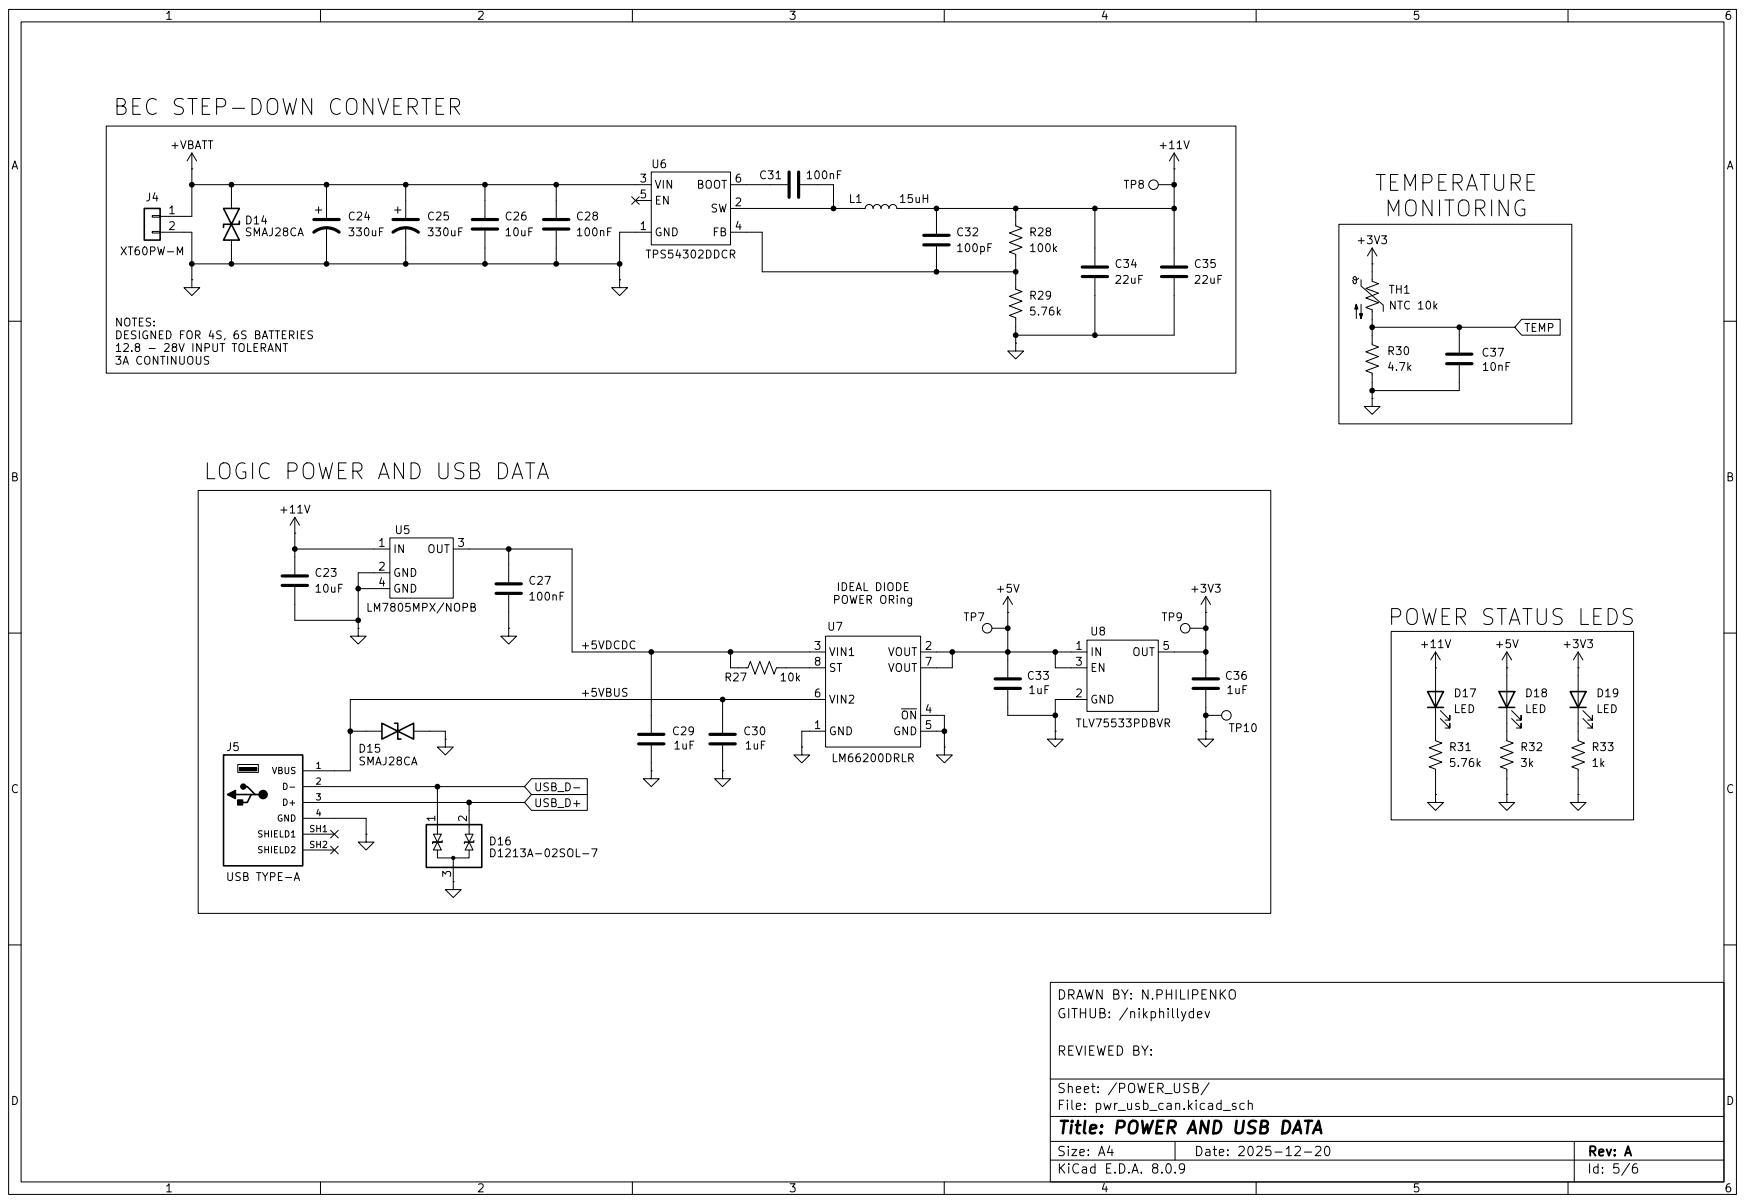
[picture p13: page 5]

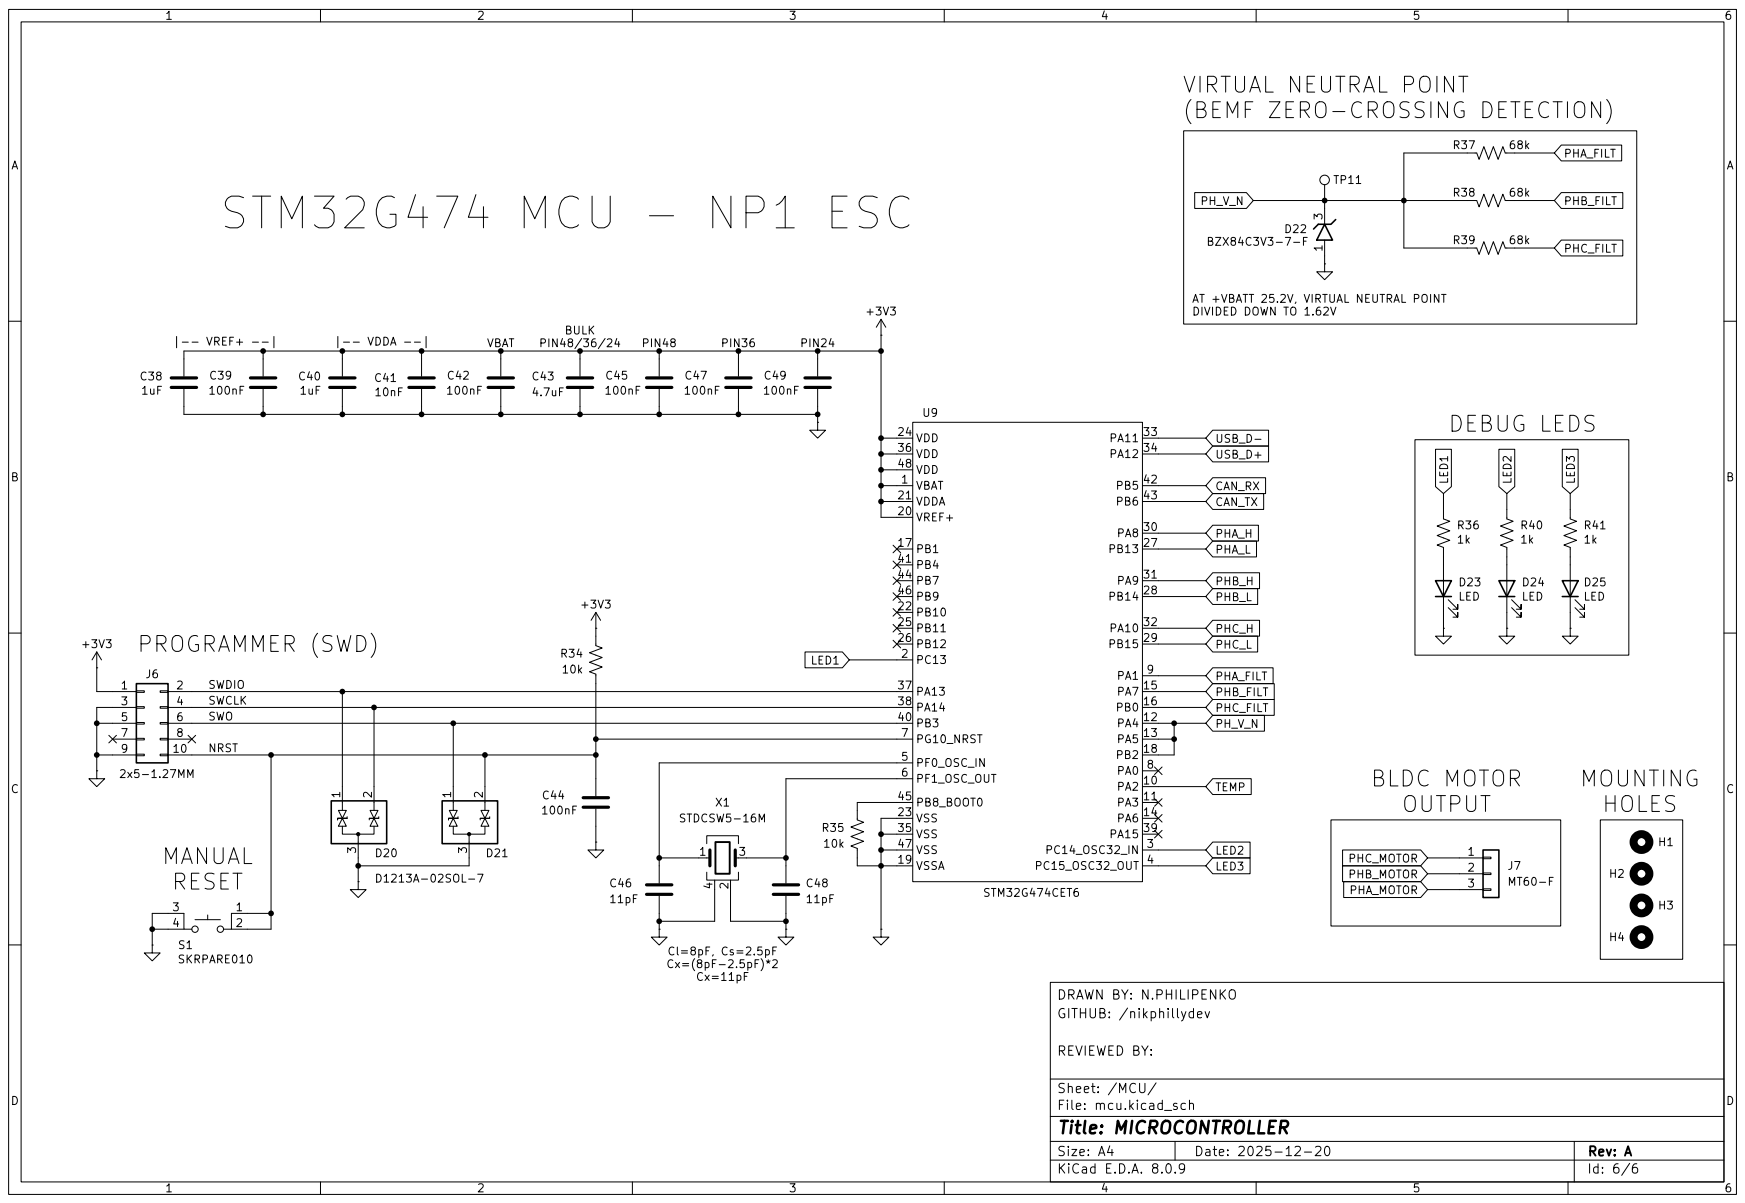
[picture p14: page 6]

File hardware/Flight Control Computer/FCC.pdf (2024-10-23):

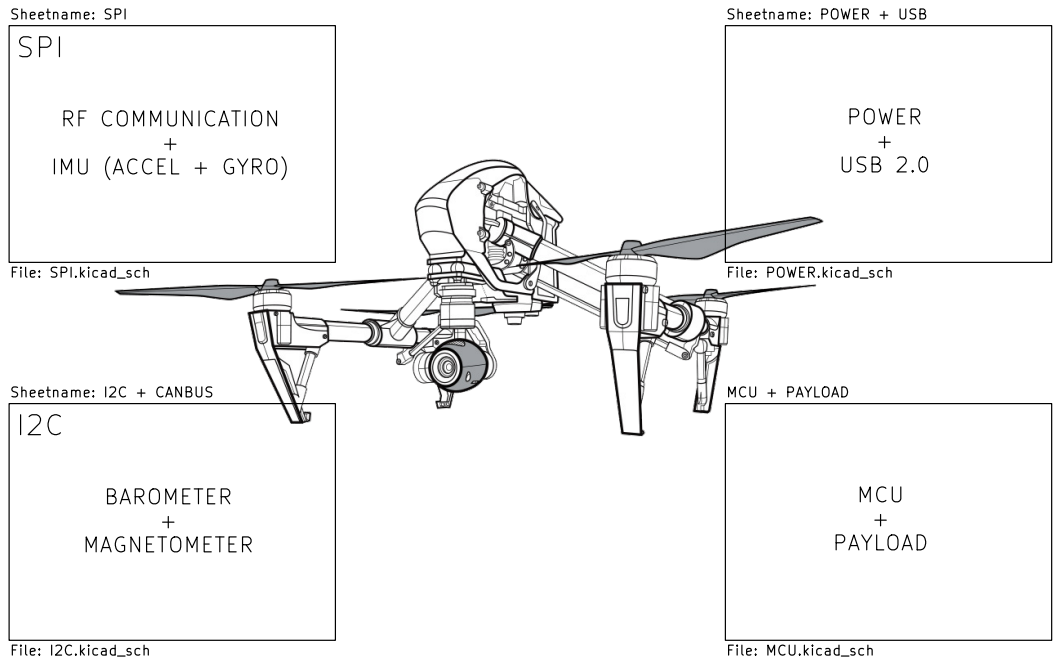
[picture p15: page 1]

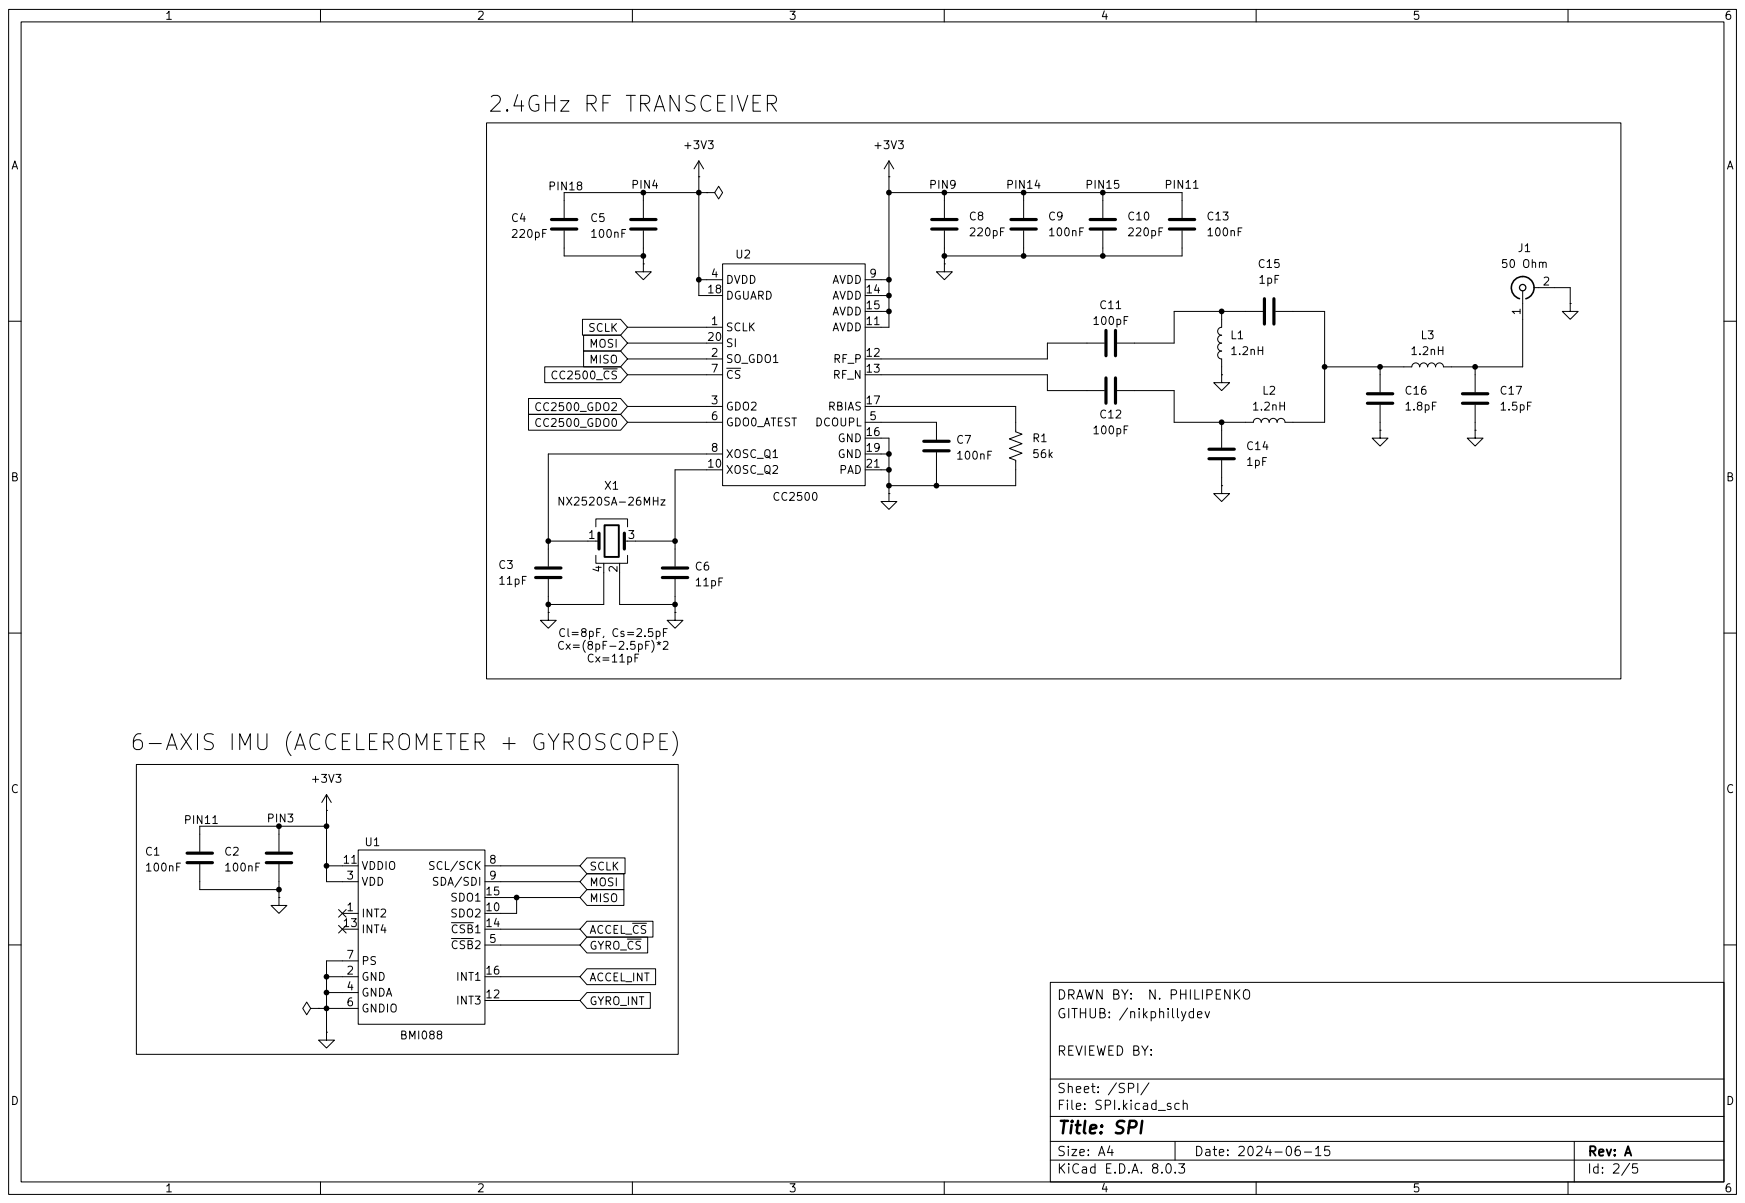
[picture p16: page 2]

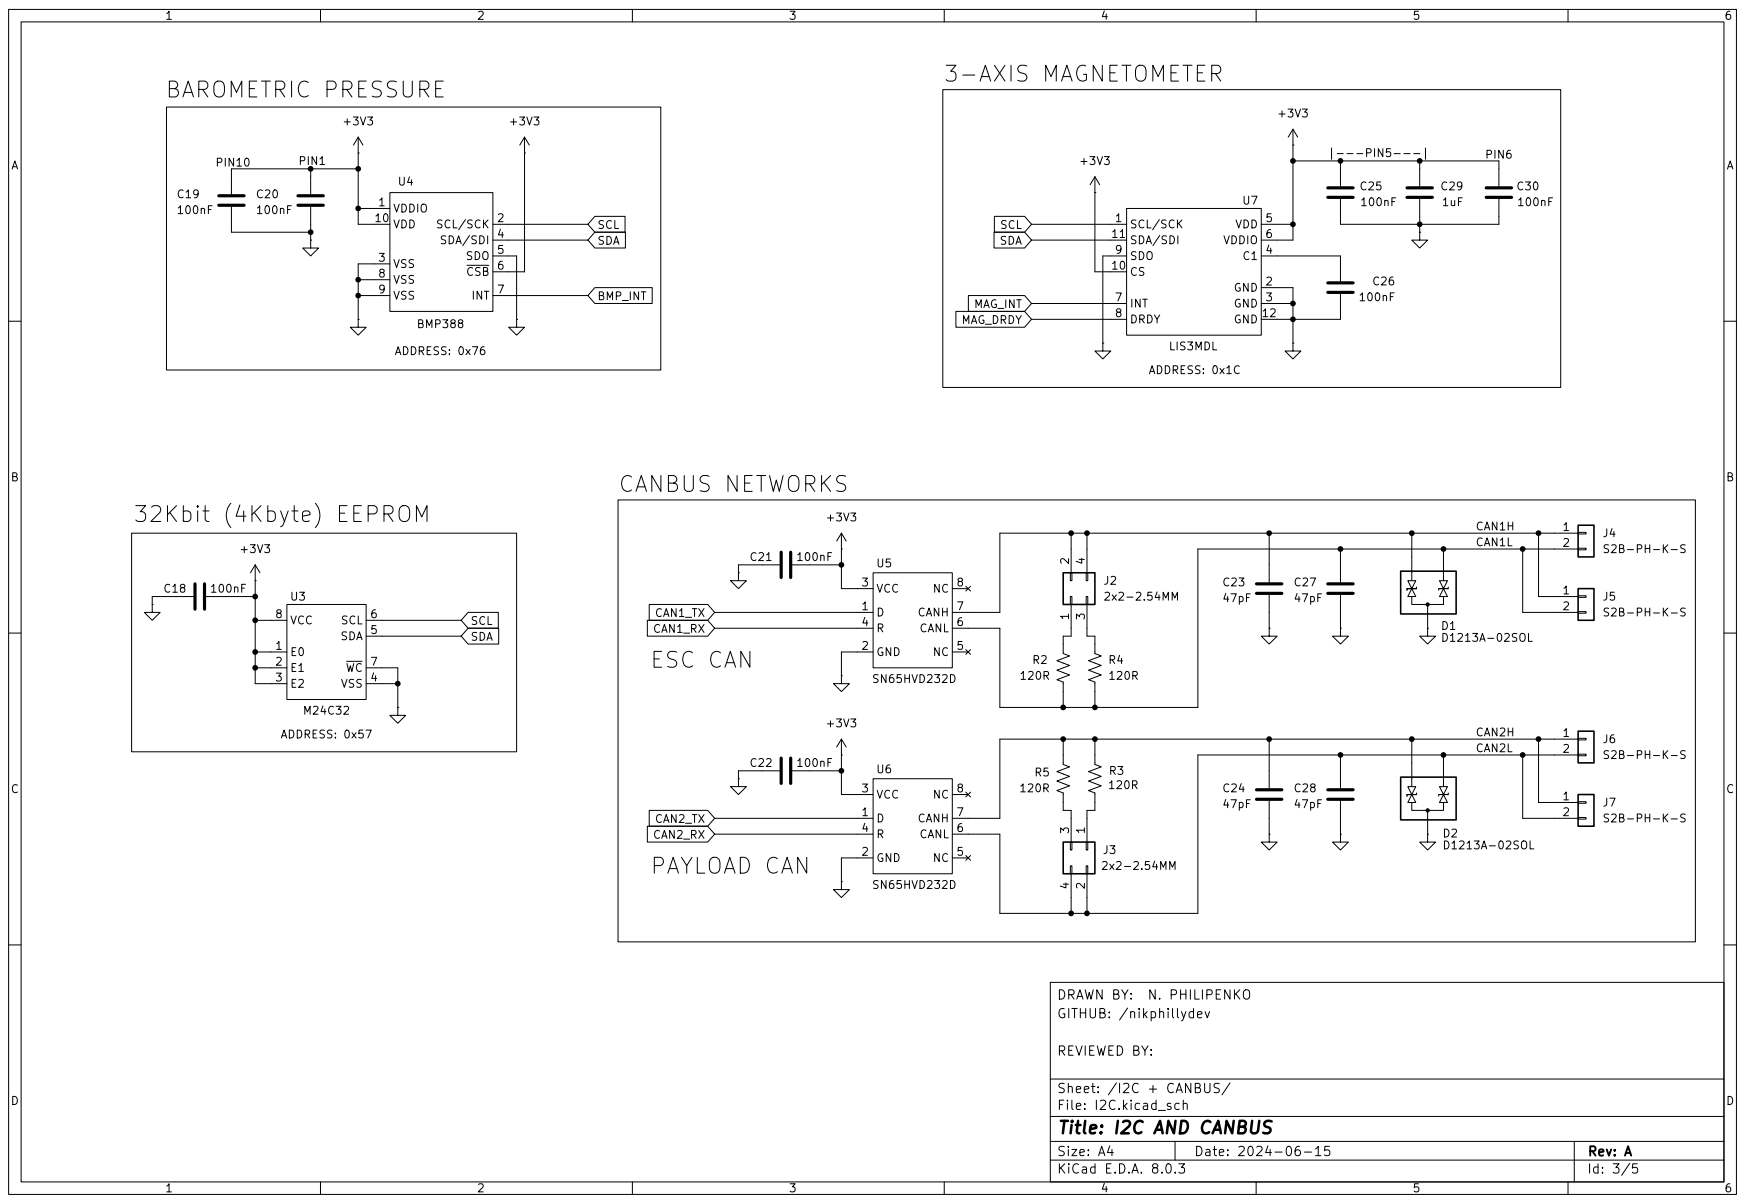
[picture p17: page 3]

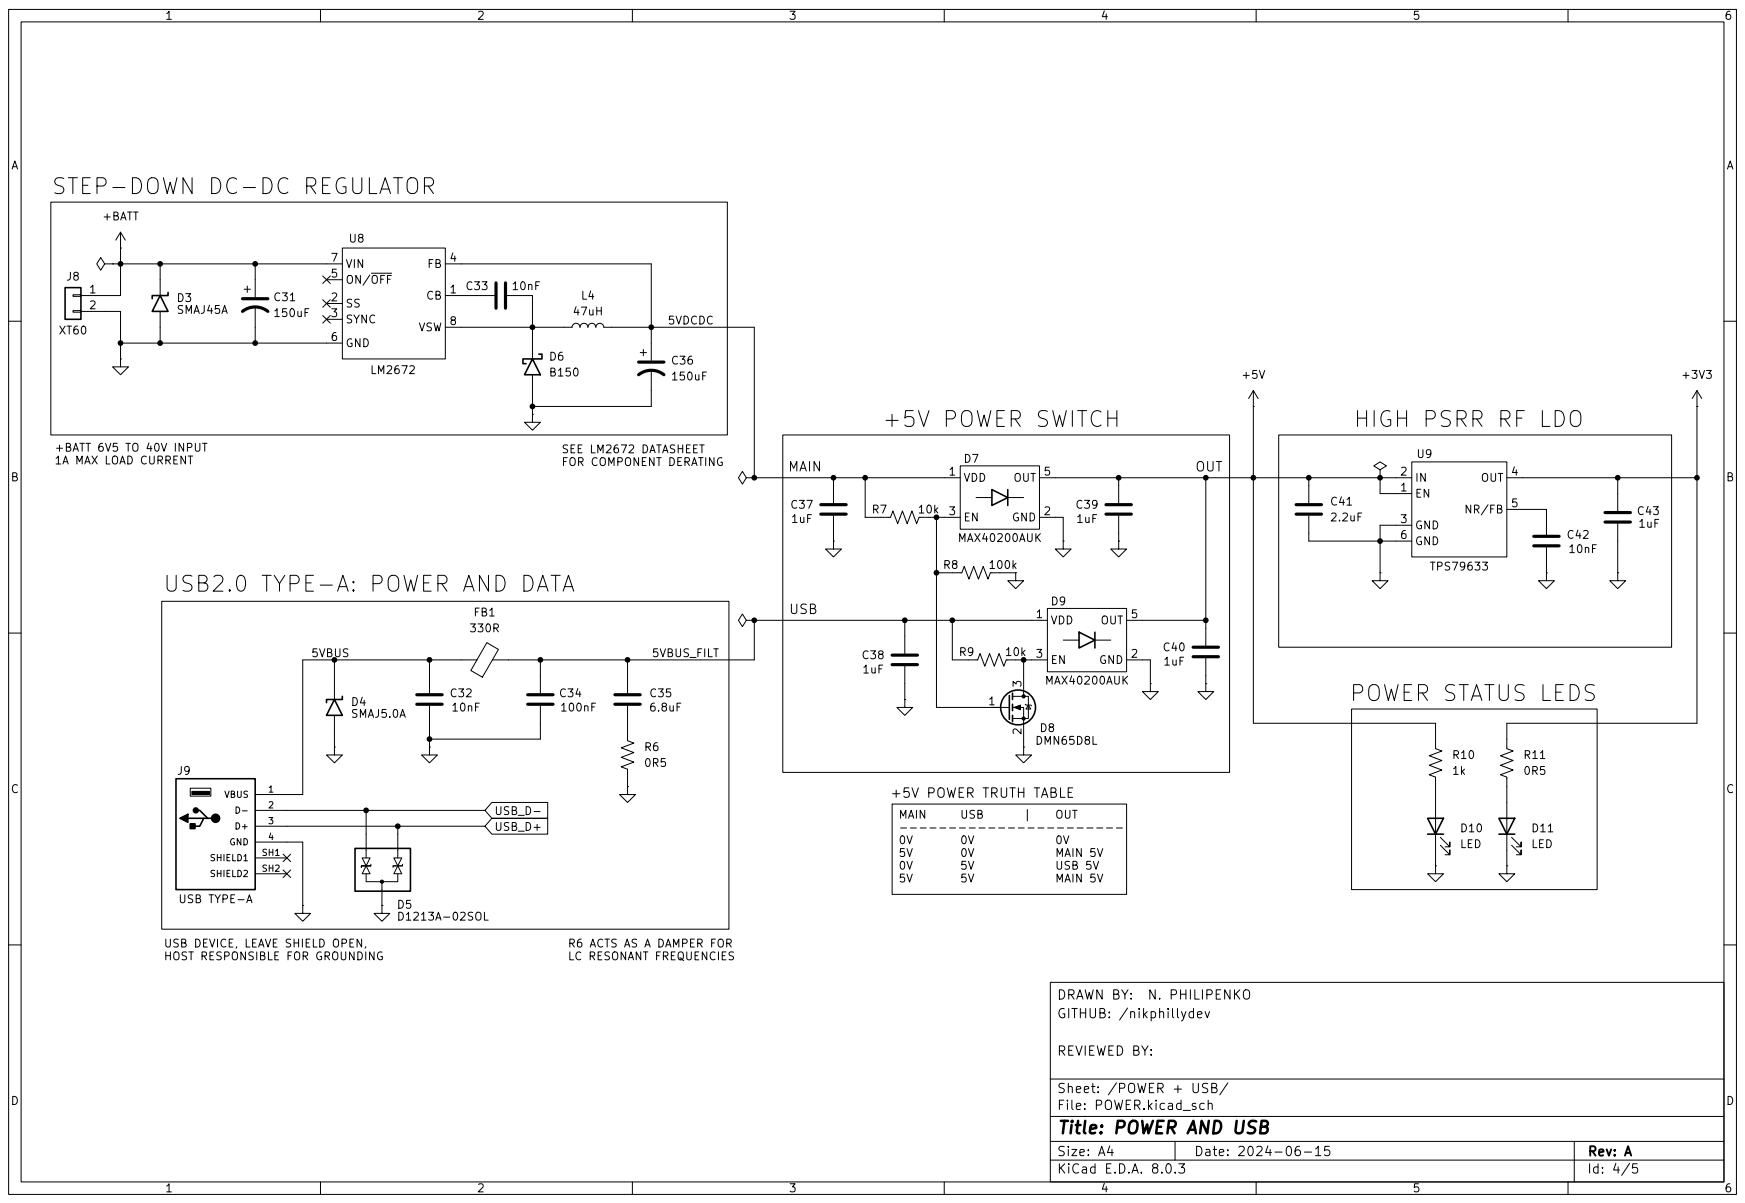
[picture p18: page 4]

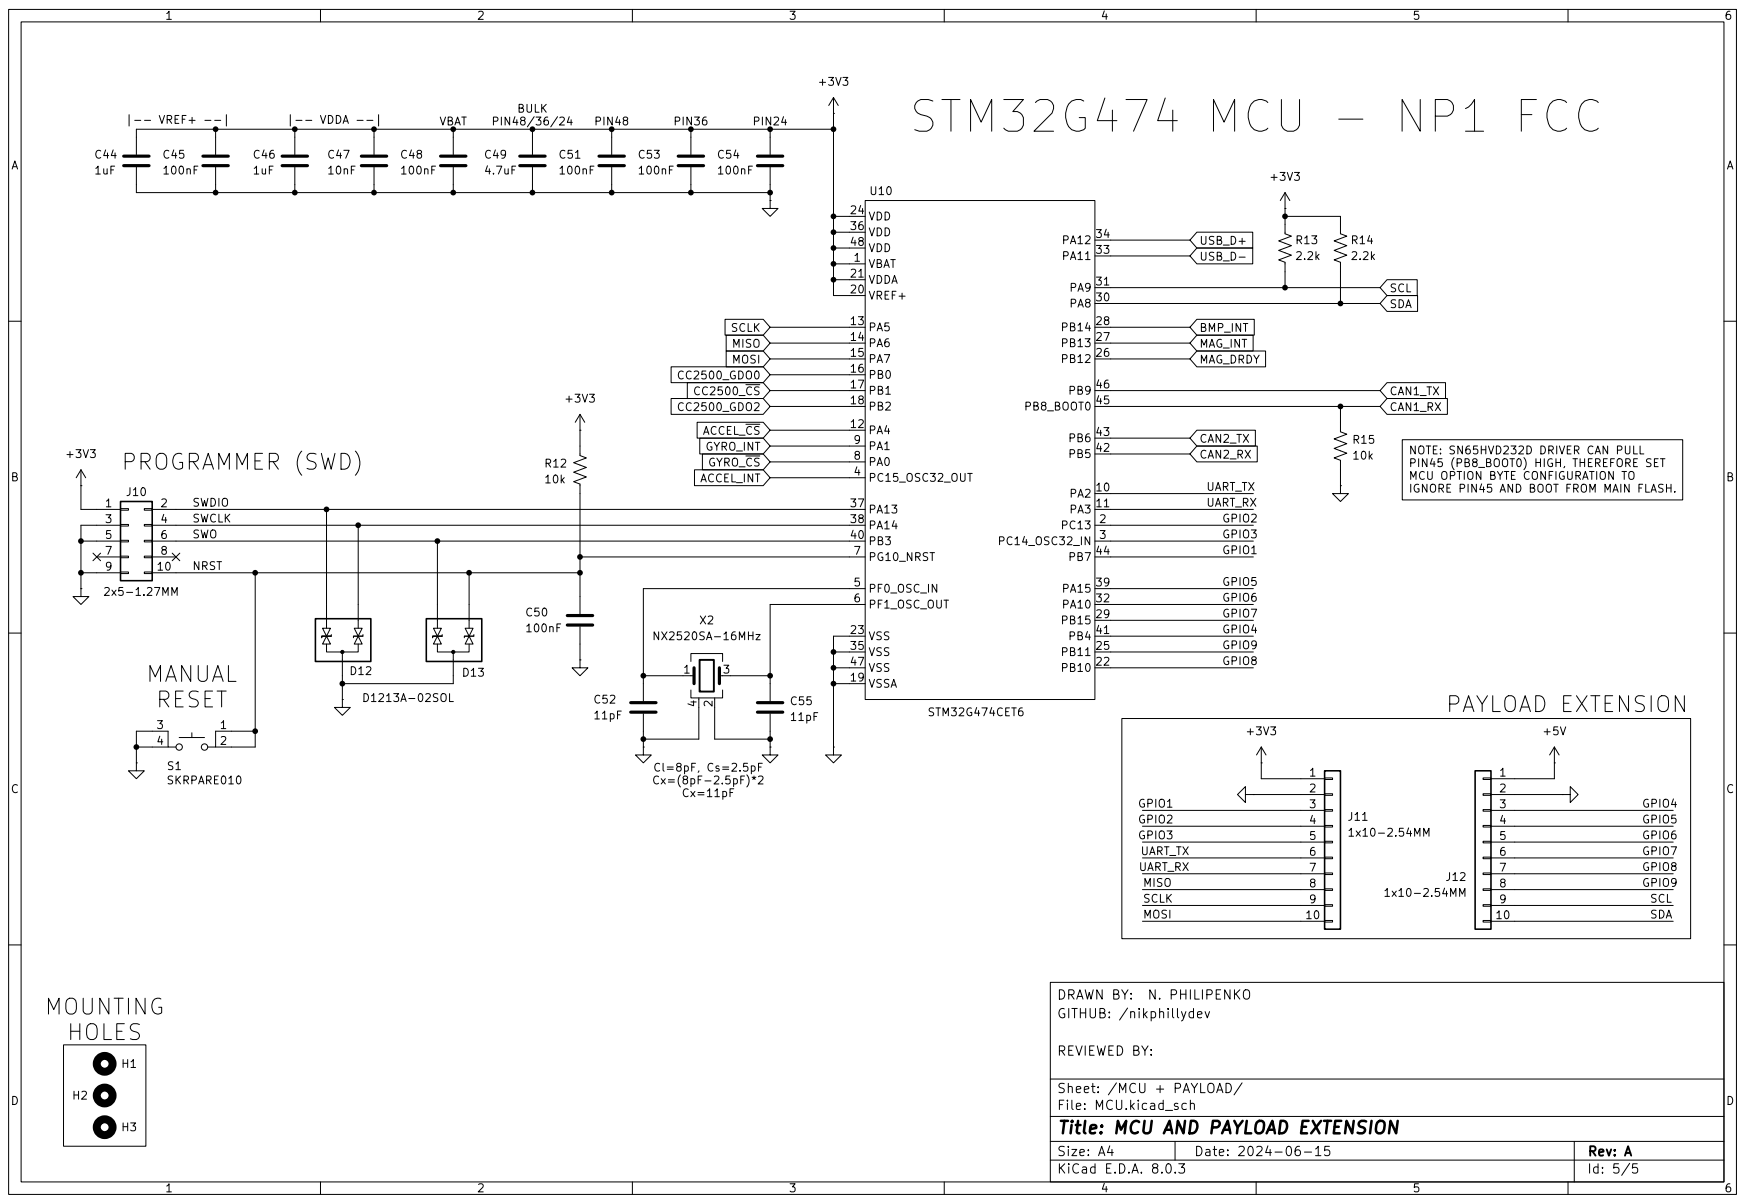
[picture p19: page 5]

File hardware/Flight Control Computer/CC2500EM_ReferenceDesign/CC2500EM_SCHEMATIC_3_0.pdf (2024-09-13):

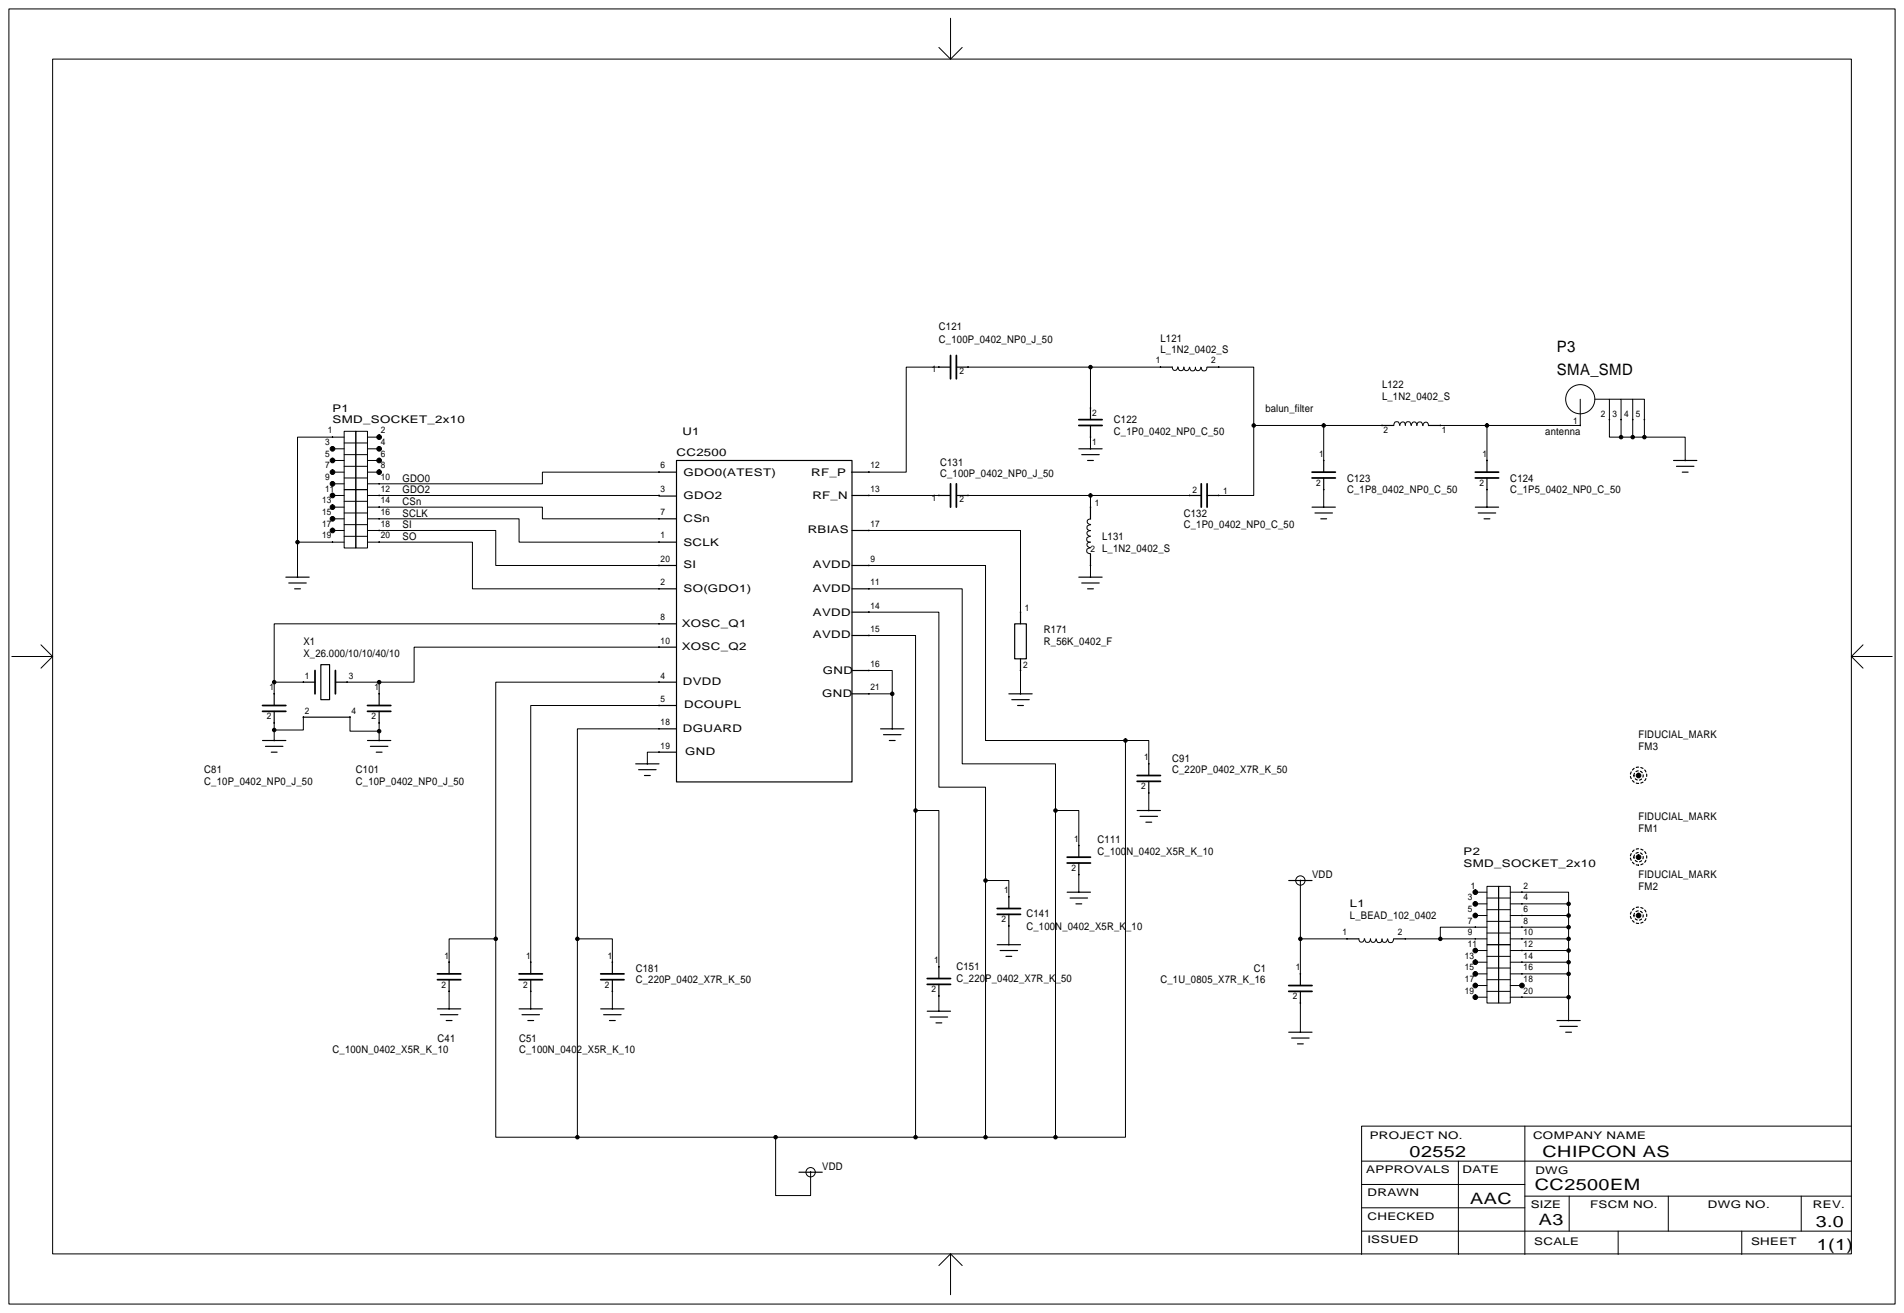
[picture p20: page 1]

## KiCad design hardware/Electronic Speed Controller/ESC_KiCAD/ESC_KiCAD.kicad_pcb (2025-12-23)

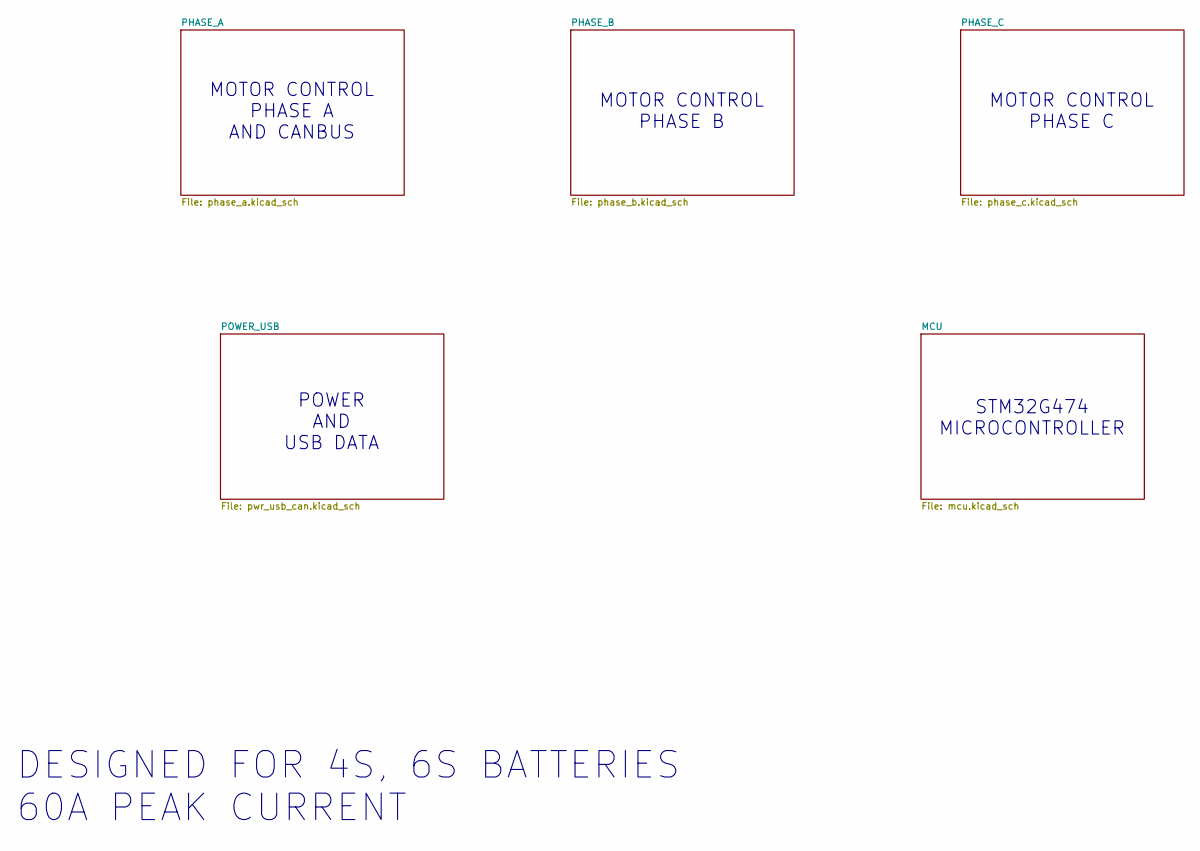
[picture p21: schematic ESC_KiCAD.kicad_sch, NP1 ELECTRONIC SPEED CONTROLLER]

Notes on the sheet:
MOTOR CONTROL PHASE C
POWER AND USB DATA
STM32G474 MICROCONTROLLER
MOTOR CONTROL PHASE B
DESIGNED FOR 4S, 6S BATTERIES 60A PEAK CURRENT
MOTOR CONTROL PHASE A AND CANBUS

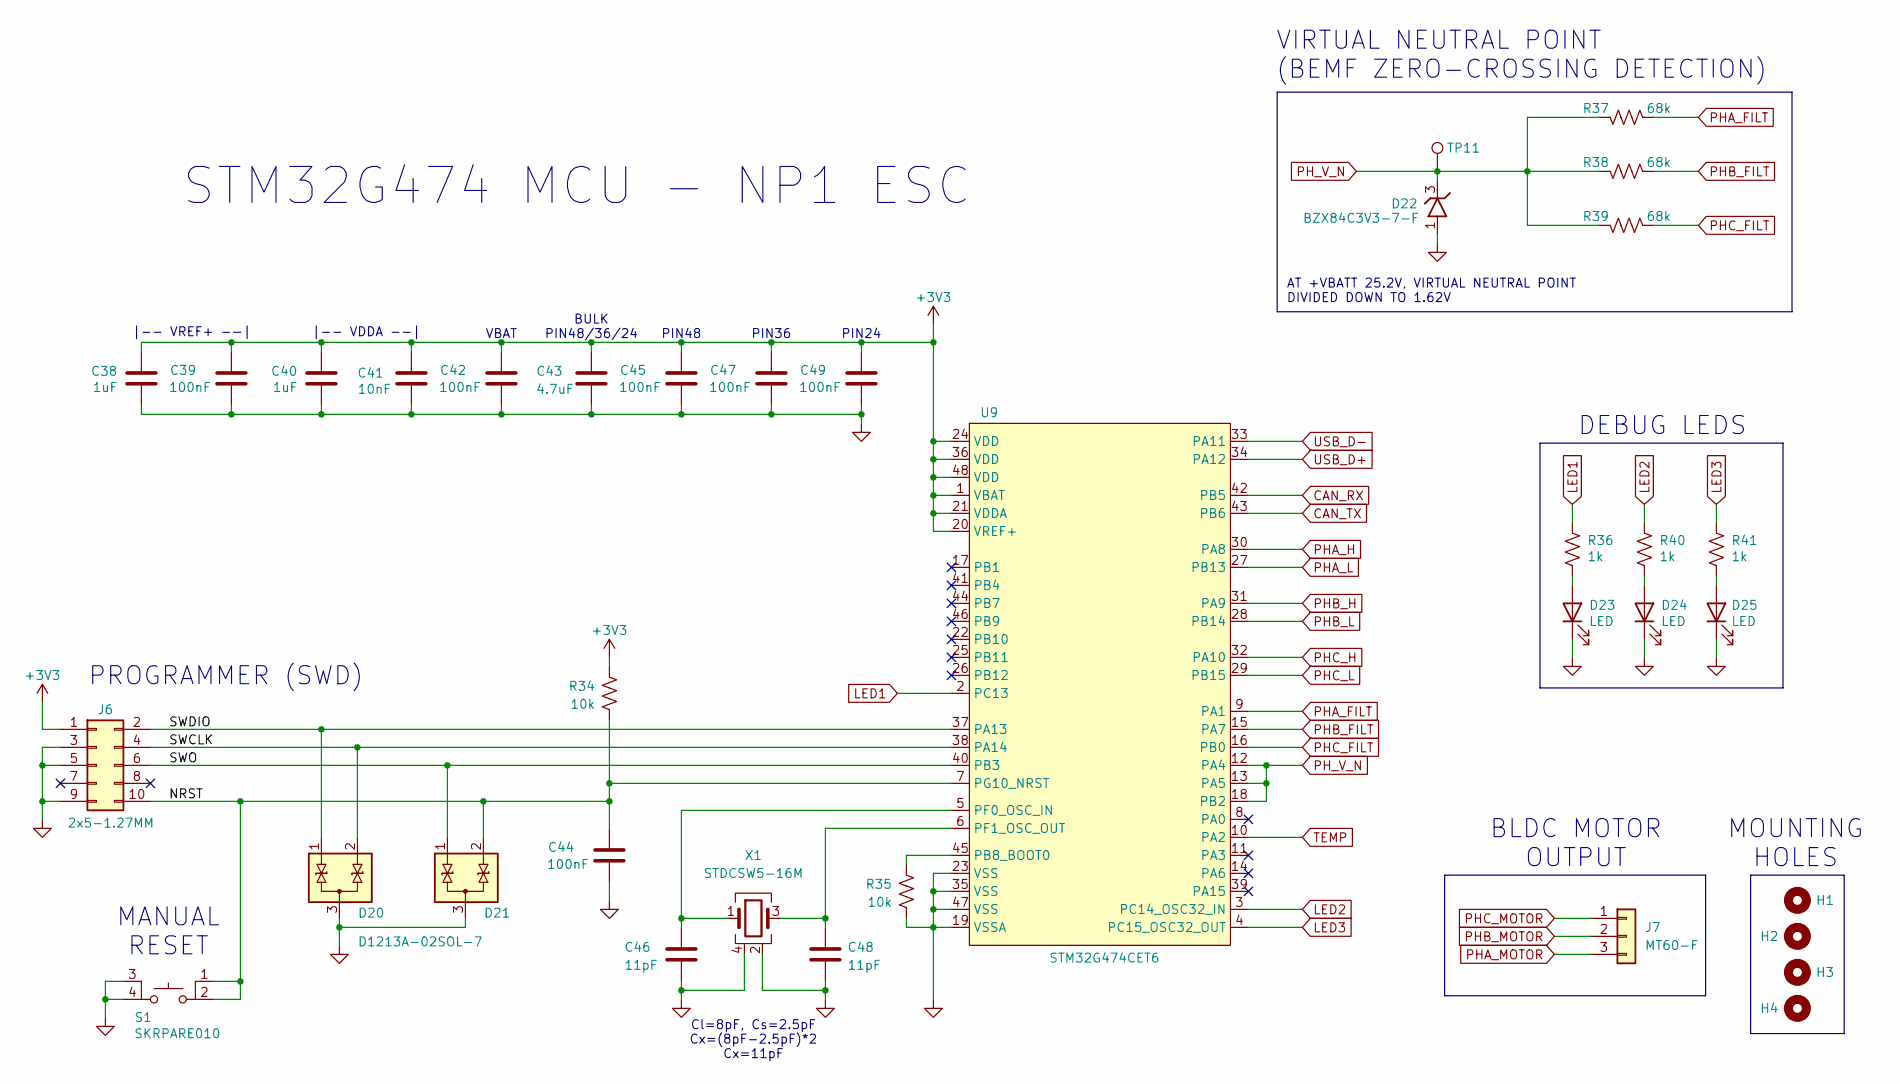
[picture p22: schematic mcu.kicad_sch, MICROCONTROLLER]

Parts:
C38, C40: 1uF; CAP_0805_2012Metric; Manufacturer Part # CL21B105KBFNNNE; JLCPCB Part # C28323
C39, C42, C44, C45, C47, C49: 100nF; CAP_0603_1608Metric; Manufacturer Part # CC0603KRX7R9BB104; JLCPCB Part # C14663
C41: 10nF; CAP_0603_1608Metric; Manufacturer Part # CL10B103KB8NNNC; JLCPCB Part # C57112
C43: 4.7uF; CAP_0805_2012Metric; Manufacturer Part # CL21A475KAQNNNE; JLCPCB Part # C1779
C46, C48: 11pF; CAP_0402_1005Metric; Manufacturer Part # GCM1555C1H110JA16D; JLCPCB Part # C710643
D20, D21: D1213A-02SOL-7; DiodesINC_SOT23-3; Manufacturer Part # D1213A-02SOL-7; JLCPCB Part # C460585
D22: BZX84C3V3-7-F; DiodesINC_SOT23-3; Manufacturer Part # BZX84C3V3-7-F; JLCPCB Part # C177019
D23, D24, D25: LED; LED_0603_1608Metric; Manufacturer Part # EAST16086YA4; JLCPCB Part # C72038
H1, H2, H3, H4: MountingHole; MountingHole_3.2mm_M3_ISO7380_Pad
J6: 2x5-1.27MM; CONN_MALE_SMT_1.27MM_2x5; Manufacturer Part # 20021121-00010C4LF; JLCPCB Part # C150517
J7: MT60-F; CONN_MALE_TH_MT60; Manufacturer Part # MT60-F; JLCPCB Part # C40020701
R34, R35: 10k; RES_0603_1608Metric; Manufacturer Part # RMCF0603FT10K0; JLCPCB Part # C25804
R36, R40, R41: 1k; RES_0603_1608Metric; Manufacturer Part # RMCF0603FT1K00; JLCPCB Part # C21190
R37, R38, R39: 68k; RES_0603_1608Metric; Manufacturer Part # ERJ-3EKF6802V; JLCPCB Part # C23231
S1: SKRPARE010; TACT_SKRP; Manufacturer Part # SKRPARE010; JLCPCB Part # C341730
TP11: TestPoint; TestPoint_THTPad_D2.5mm_Drill1.2mm
U9: STM32G474CET6; STM_LQFP48; Manufacturer Part # STM32G474CET6; JLCPCB Part # C730125
X1: STDCSW5-16M; NDK_NX2520SA; Manufacturer Part # STDCSW5-16M; JLCPCB Part # C280836

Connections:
+3V3: C38.2, C39.2, C40.2, C41.2, C42.2, C43.1, C45.2, C47.2, C49.2, J6.1, R34.1, U9.1 (VBAT), U9.20 (VREF+), U9.21 (VDDA), U9.24 (VDD), U9.36 (VDD), U9.48 (VDD); also elsewhere on the board
/MCU/NRST: C44.2, D21.2 (K), J6.10, R34.2, S1.1, S1.2, U9.7 (PG10_NRST)
/MCU/SWCLK: D20.2 (K), J6.4, U9.38 (PA14)
/MCU/SWDIO: D20.1 (K), J6.2, U9.37 (PA13)
/MCU/SWO: D21.1 (K), J6.6, U9.40 (PB3)
CAN_RX: U9.42 (PB5); also elsewhere on the board
CAN_TX: U9.43 (PB6); also elsewhere on the board
GND: C38.1, C39.1, C40.1, C41.1, C42.1, C43.2, C44.1, C45.1, C46.2, C47.1, C48.2, C49.1, D20.3 (A), D21.3 (A), D22.1 (A), D23.1 (K), D24.1 (K), D25.1 (K), J6.3, J6.5, J6.9, R35.2, S1.3, S1.4, U9.19 (VSSA), U9.23 (VSS), U9.35 (VSS), U9.47 (VSS), X1.2, X1.4; also elsewhere on the board
LED1: R36.1, U9.2 (PC13)
LED2: R40.1, U9.3 (PC14_OSC32_IN)
LED3: R41.1, U9.4 (PC15_OSC32_OUT)
unnamed: D23.2 (A), R36.2
unnamed: D24.2 (A), R40.2
unnamed: D25.2 (A), R41.2
unnamed: R35.1, U9.45 (PB8_BOOT0)
unnamed: C46.1, U9.5 (PF0_OSC_IN), X1.1
unnamed: C48.1, U9.6 (PF1_OSC_OUT), X1.3
PHA_FILT: R37.2, U9.9 (PA1); also elsewhere on the board
PHA_H: U9.30 (PA8); also elsewhere on the board
PHA_L: U9.27 (PB13); also elsewhere on the board
PHA_MOTOR: J7.3; also elsewhere on the board
PHB_FILT: R38.2, U9.15 (PA7); also elsewhere on the board
PHB_H: U9.31 (PA9); also elsewhere on the board
PHB_L: U9.28 (PB14); also elsewhere on the board
PHB_MOTOR: J7.2; also elsewhere on the board
PHC_FILT: R39.2, U9.16 (PB0); also elsewhere on the board
PHC_H: U9.32 (PA10); also elsewhere on the board
PHC_L: U9.29 (PB15); also elsewhere on the board
PHC_MOTOR: J7.1; also elsewhere on the board
PH_V_N: D22.3 (K), R37.1, R38.1, R39.1, TP11.1, U9.12 (PA4), U9.13 (PA5), U9.18 (PB2)
TEMP: U9.10 (PA2); also elsewhere on the board
USB_D+: U9.34 (PA12); also elsewhere on the board
USB_D-: U9.33 (PA11); also elsewhere on the board

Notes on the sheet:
MANUAL RESET
MOUNTING HOLES
BULK PIN48/36/24
VIRTUAL NEUTRAL POINT (BEMF ZERO-CROSSING DETECTION)
VBAT
Cl=8pF, Cs=2.5pF Cx=(8pF-2.5pF)*2 Cx=11pF
AT +VBATT 25.2V, VIRTUAL NEUTRAL POINT DIVIDED DOWN TO 1.62V
PIN24
PIN36
DEBUG LEDS
PROGRAMMER (SWD)
BLDC MOTOR OUTPUT
|-- VREF+ --|
STM32G474 MCU - NP1 ESC
|-- VDDA --|
PIN48

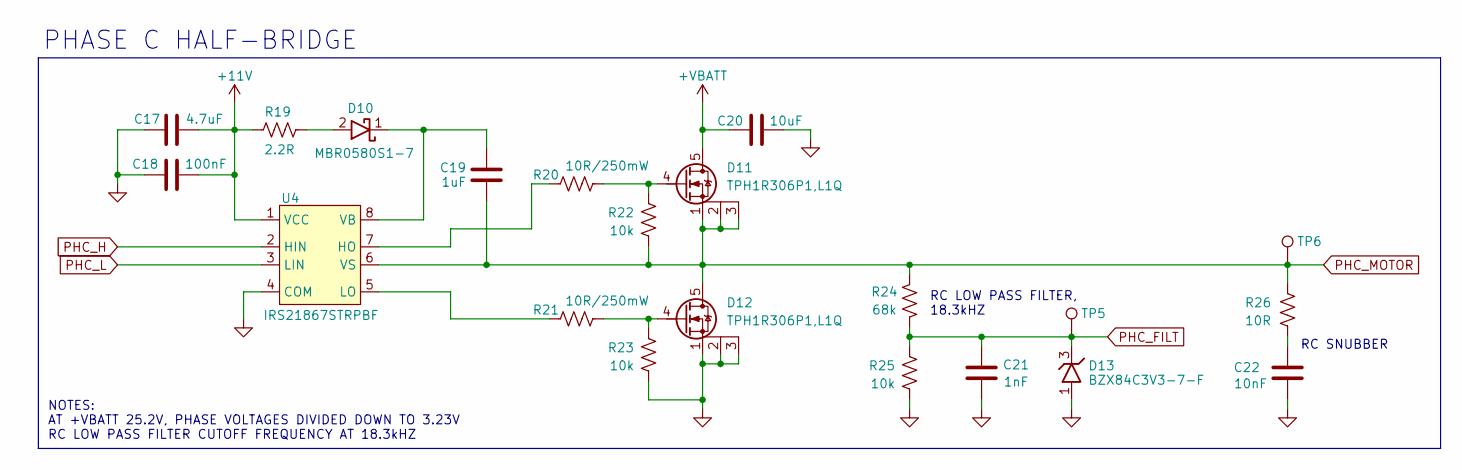
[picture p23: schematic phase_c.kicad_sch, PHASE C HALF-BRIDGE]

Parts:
C17: 4.7uF; CAP_0805_2012Metric; Manufacturer Part # CL21A475KAQNNNE; JLCPCB Part # C1779
C18: 100nF; CAP_0603_1608Metric; Manufacturer Part # CC0603KRX7R9BB104; JLCPCB Part # C14663
C19: 1uF; CAP_0805_2012Metric; Manufacturer Part # CL21B105KBFNNNE; JLCPCB Part # C28323
C20: 10uF; CAP_1206_3216Metric; Manufacturer Part # CL31A106KBHNNNE; JLCPCB Part # C13585
C21: 1nF; CAP_0603_1608Metric; Manufacturer Part # CL10B102KB8NNNC; JLCPCB Part # C1588
C22: 10nF; CAP_0603_1608Metric; Manufacturer Part # CL10B103KB8NNNC; JLCPCB Part # C57112
D10: MBR0580S1-7; DiodesINC_SOD123; Manufacturer Part # MBR0580S1-7; JLCPCB Part # C177047
D11, D12: TPH1R306P1,L1Q; PQFN-8-EP_6x5mm_P1.27mm_Generic; Manufacturer Part # TPH1R306P1,L1Q; JLCPCB Part # C6290261
D13: BZX84C3V3-7-F; DiodesINC_SOT23-3; Manufacturer Part # BZX84C3V3-7-F; JLCPCB Part # C177019
R19: 2.2R; RES_1206_3216Metric; Manufacturer Part # CRCW12062R20FKEAHP; JLCPCB Part # C1854860
R20, R21: 10R/250mW; RES_0805_2012Metric; Manufacturer Part # AC0805FR-7W10RL; JLCPCB Part # C727983
R22, R23, R25: 10k; RES_0603_1608Metric; Manufacturer Part # RMCF0603FT10K0; JLCPCB Part # C25804
R24: 68k; RES_0603_1608Metric; Manufacturer Part # ERJ-3EKF6802V; JLCPCB Part # C23231
R26: 10R; RES_0603_1608Metric; Manufacturer Part # RC0603FR-0710RL; JLCPCB Part # C22859
TP5, TP6: TestPoint; TestPoint_THTPad_D2.5mm_Drill1.2mm
U4: IRS21867STRPBF; SOIC-8; Manufacturer Part # IRS21867STRPBF; JLCPCB Part # C52290

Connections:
+11V: C17.2, C18.2, R19.1, U4.1 (VCC); also elsewhere on the board
+VBATT: C20.1, D11.5 (D); also elsewhere on the board
GND: C17.1, C18.1, C20.2, C21.1, C22.1, D12.1 (S), D12.2 (S), D12.3 (S), D13.1 (A), R23.2, R25.2, U4.4 (COM); also elsewhere on the board
unnamed: C22.2, R26.2
unnamed: D10.2 (A), R19.2
unnamed: C19.2, D10.1 (K), U4.8 (VB)
unnamed: D11.4 (G), R20.2, R22.1
unnamed: D12.4 (G), R21.2, R23.1
unnamed: R20.1, U4.7 (HO)
unnamed: R21.1, U4.5 (LO)
PHC_FILT: C21.2, D13.3 (K), R24.1, R25.1, TP5.1; also elsewhere on the board
PHC_H: U4.2 (HIN); also elsewhere on the board
PHC_L: U4.3 (LIN); also elsewhere on the board
PHC_MOTOR: C19.1, D11.1 (S), D11.2 (S), D11.3 (S), D12.5 (D), R22.2, R24.2, R26.1, TP6.1, U4.6 (VS); also elsewhere on the board

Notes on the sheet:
RC SNUBBER
NOTES: AT +VBATT 25.2V, PHASE VOLTAGES DIVIDED DOWN TO 3.23V RC LOW PASS FILTER CUTOFF FREQUENCY AT 18.3kHZ
RC LOW PASS FILTER, 18.3kHZ
PHASE C HALF-BRIDGE

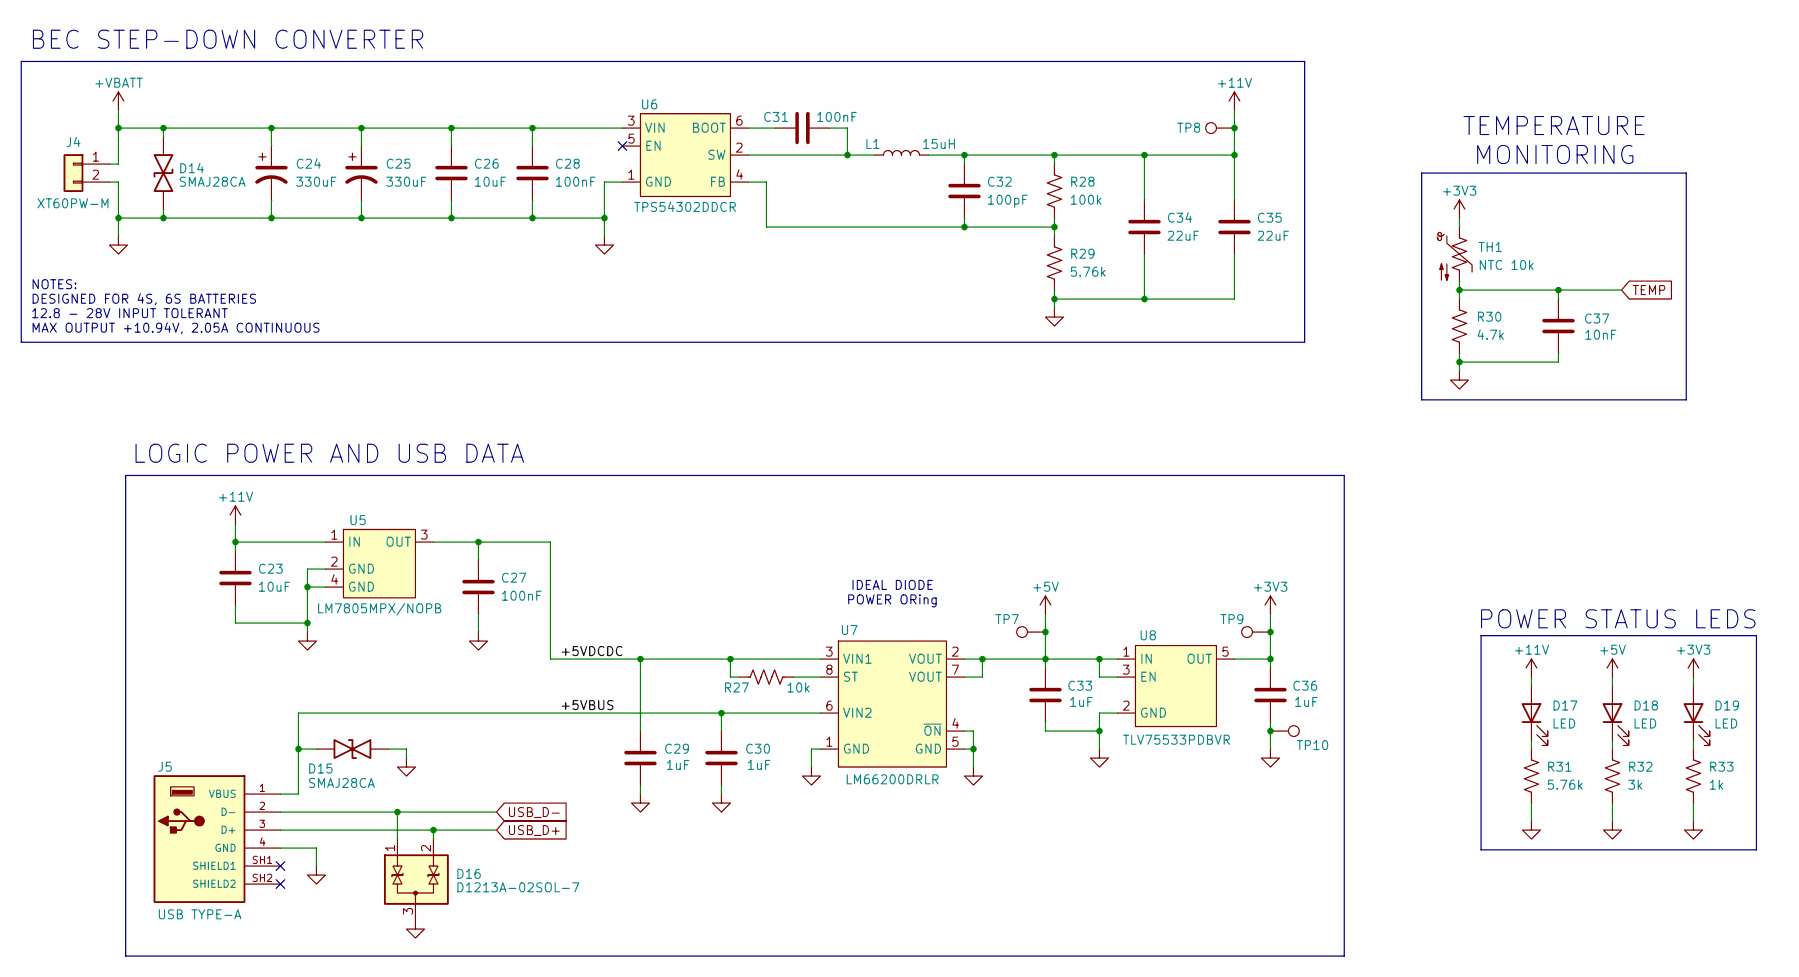
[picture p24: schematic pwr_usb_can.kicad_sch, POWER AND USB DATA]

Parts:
C23, C26: 10uF; CAP_1206_3216Metric; Manufacturer Part # CL31A106KBHNNNE; JLCPCB Part # C13585
C24, C25: 330uF; CAP_ALUM_HORIZONTAL; Manufacturer Part # 35ZLH330MEFC10X12.5; JLCPCB Part # C75177
C27, C28, C31: 100nF; CAP_0603_1608Metric; Manufacturer Part # CC0603KRX7R9BB104; JLCPCB Part # C14663
C29, C30, C33, C36: 1uF; CAP_0805_2012Metric; Manufacturer Part # CL21B105KBFNNNE; JLCPCB Part # C28323
C32: 100pF; CAP_0603_1608Metric; Manufacturer Part # CL10C101JB8NNNC; JLCPCB Part # C14858
C34, C35: 22uF; CAP_0805_2012Metric; Manufacturer Part # CL21A226MAYNNNE; JLCPCB Part # C45783
C37: 10nF; CAP_0603_1608Metric; Manufacturer Part # CL10B103KB8NNNC; JLCPCB Part # C57112
D14, D15: SMAJ28CA; Littelfuse_SMA; Manufacturer Part # SMAJ28CA; JLCPCB Part # C148228
D16: D1213A-02SOL-7; DiodesINC_SOT23-3; Manufacturer Part # D1213A-02SOL-7; JLCPCB Part # C460585
D17, D18, D19: LED; LED_0603_1608Metric; Manufacturer Part # EAST16086YA4; JLCPCB Part # C72038
J4: XT60PW-M; CONN_MALE_TH_XT60PW; Manufacturer Part # XT60PW-M; JLCPCB Part # C98732
J5: USB TYPE-A; USB2.0_4P_AMPHENOL_87583-2010BLF; Manufacturer Part # 87583-2010BLF; JLCPCB Part # C599118
L1: 15uH; L_6045S; Manufacturer Part # SWPA6045S150MT; JLCPCB Part # C83374
R27: 10k; RES_0603_1608Metric; Manufacturer Part # RMCF0603FT10K0; JLCPCB Part # C25804
R28: 100k; RES_0603_1608Metric; Manufacturer Part # RC0603FR-07100KL; JLCPCB Part # C25803
R29, R31: 5.76k; RES_0603_1608Metric; Manufacturer Part # RC0603FR-075K76L; JLCPCB Part # C2933239
R30: 4.7k; RES_0603_1608Metric; Manufacturer Part # RC0603FR-074K7L; JLCPCB Part # C23162
R32: 3k; RES_0603_1608Metric; Manufacturer Part # RMCF0603FT3K00; JLCPCB Part # C4211
R33: 1k; RES_0603_1608Metric; Manufacturer Part # RMCF0603FT1K00; JLCPCB Part # C21190
TH1: NTC 10k; RES_0603_1608Metric; Manufacturer Part # NCU18XH103F60RB; JLCPCB Part # C440252
TP7, TP8, TP9, TP10: TestPoint; TestPoint_Pad_2.0x2.0mm
U5: LM7805MPX/NOPB; TI_SOT223-4; Manufacturer Part # LM7805MPX/NOPB; JLCPCB Part # C2848241
U6: TPS54302DDCR; TI_SOT23-6; Manufacturer Part # TPS54302DDCR; JLCPCB Part # C311983
U7: LM66200DRLR; TI_SOT-5X3; Manufacturer Part # LM66200DRLR; JLCPCB Part # C3235556
U8: TLV75533PDBVR; TI_SOT23-5; Manufacturer Part # TLV75533PDBVR; JLCPCB Part # C404027

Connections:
+3V3: C36.2, D19.2 (A), TH1.1, TP9.1, U8.5 (OUT); also elsewhere on the board
+5V: C33.2, D18.2 (A), TP7.1, U7.2 (VOUT), U7.7 (VOUT), U8.1 (IN), U8.3 (EN)
+11V: C23.1, C32.1, C34.1, C35.1, D17.2 (A), L1.2, R28.1, TP8.1, U5.1 (IN); also elsewhere on the board
+VBATT: C24.1, C25.1, C26.1, C28.2, D14.1 (K), J4.1, U6.3 (VIN); also elsewhere on the board
/POWER_USB/+5VBUS: C30.2, D15.1 (K), J5.1 (VBUS), U7.6 (VIN2)
/POWER_USB/+5VDCDC: C27.2, C29.2, R27.1, U5.3 (OUT), U7.3 (VIN1)
GND: C23.2, C24.2, C25.2, C26.2, C27.1, C28.1, C29.1, C30.1, C33.1, C34.2, C35.2, C36.1, C37.1, D14.2 (A), D15.2 (A), D16.3 (A), J4.2, J5.4 (GND), R29.2, R30.2, R31.2, R32.2, R33.2, TP10.1, U5.2 (GND), U5.4 (GND), U6.1 (GND), U7.1 (GND), U7.4 (~ON), U7.5 (GND), U8.2 (GND); also elsewhere on the board
unnamed: D17.1 (K), R31.1
unnamed: D18.1 (K), R32.1
unnamed: D19.1 (K), R33.1
unnamed: C31.1, U6.6 (BOOT)
unnamed: C32.2, R28.2, R29.1, U6.4 (FB)
unnamed: C31.2, L1.1, U6.2 (SW)
unnamed: R27.2, U7.8 (ST)
TEMP: C37.2, R30.1, TH1.2; also elsewhere on the board
USB_D+: D16.2 (K), J5.3 (D+); also elsewhere on the board
USB_D-: D16.1 (K), J5.2 (D-); also elsewhere on the board

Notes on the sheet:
POWER STATUS LEDS
LOGIC POWER AND USB DATA
IDEAL DIODE POWER ORing
TEMPERATURE MONITORING
NOTES: DESIGNED FOR 4S, 6S BATTERIES 12.8 - 28V INPUT TOLERANT MAX OUTPUT +10.94V, 2.05A CONTINUOUS
BEC STEP-DOWN CONVERTER

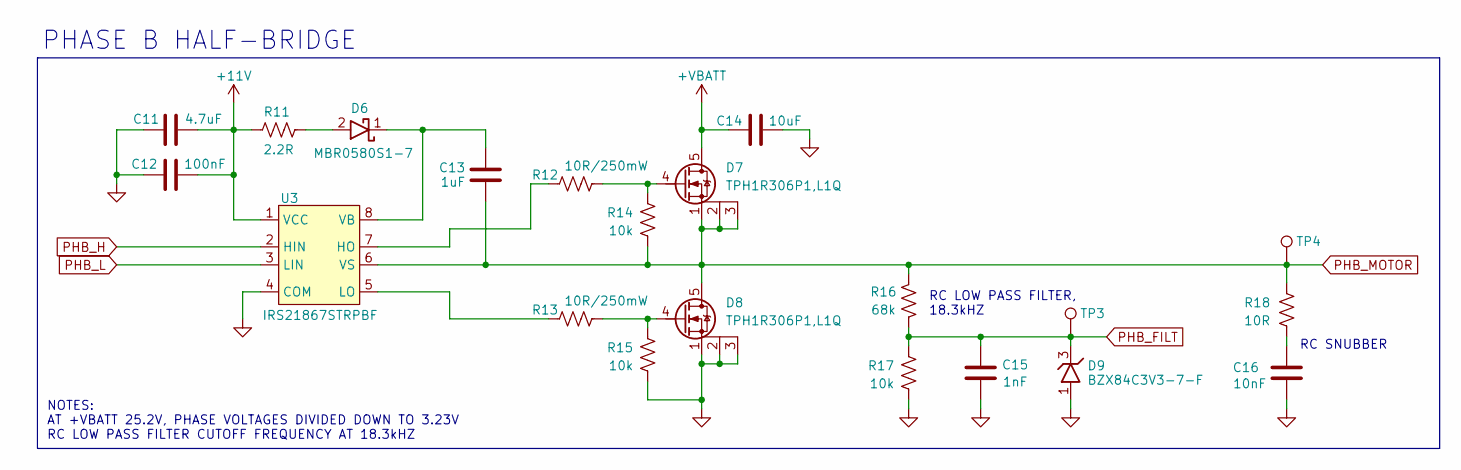
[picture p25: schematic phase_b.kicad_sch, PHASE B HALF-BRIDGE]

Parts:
C11: 4.7uF; CAP_0805_2012Metric; Manufacturer Part # CL21A475KAQNNNE; JLCPCB Part # C1779
C12: 100nF; CAP_0603_1608Metric; Manufacturer Part # CC0603KRX7R9BB104; JLCPCB Part # C14663
C13: 1uF; CAP_0805_2012Metric; Manufacturer Part # CL21B105KBFNNNE; JLCPCB Part # C28323
C14: 10uF; CAP_1206_3216Metric; Manufacturer Part # CL31A106KBHNNNE; JLCPCB Part # C13585
C15: 1nF; CAP_0603_1608Metric; Manufacturer Part # CL10B102KB8NNNC; JLCPCB Part # C1588
C16: 10nF; CAP_0603_1608Metric; Manufacturer Part # CL10B103KB8NNNC; JLCPCB Part # C57112
D6: MBR0580S1-7; DiodesINC_SOD123; Manufacturer Part # MBR0580S1-7; JLCPCB Part # C177047
D7, D8: TPH1R306P1,L1Q; PQFN-8-EP_6x5mm_P1.27mm_Generic; Manufacturer Part # TPH1R306P1,L1Q; JLCPCB Part # C6290261
D9: BZX84C3V3-7-F; DiodesINC_SOT23-3; Manufacturer Part # BZX84C3V3-7-F; JLCPCB Part # C177019
R11: 2.2R; RES_1206_3216Metric; Manufacturer Part # CRCW12062R20FKEAHP; JLCPCB Part # C1854860
R12, R13: 10R/250mW; RES_0805_2012Metric; Manufacturer Part # AC0805FR-7W10RL; JLCPCB Part # C727983
R14, R15, R17: 10k; RES_0603_1608Metric; Manufacturer Part # RMCF0603FT10K0; JLCPCB Part # C25804
R16: 68k; RES_0603_1608Metric; Manufacturer Part # ERJ-3EKF6802V; JLCPCB Part # C23231
R18: 10R; RES_0603_1608Metric; Manufacturer Part # RC0603FR-0710RL; JLCPCB Part # C22859
TP3, TP4: TestPoint; TestPoint_THTPad_D2.5mm_Drill1.2mm
U3: IRS21867STRPBF; SOIC-8; Manufacturer Part # IRS21867STRPBF; JLCPCB Part # C52290

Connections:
+11V: C11.2, C12.2, R11.1, U3.1 (VCC); also elsewhere on the board
+VBATT: C14.1, D7.5 (D); also elsewhere on the board
GND: C11.1, C12.1, C14.2, C15.1, C16.1, D8.1 (S), D8.2 (S), D8.3 (S), D9.1 (A), R15.2, R17.2, U3.4 (COM); also elsewhere on the board
unnamed: C16.2, R18.2
unnamed: D6.2 (A), R11.2
unnamed: C13.2, D6.1 (K), U3.8 (VB)
unnamed: D7.4 (G), R12.2, R14.1
unnamed: D8.4 (G), R13.2, R15.1
unnamed: R12.1, U3.7 (HO)
unnamed: R13.1, U3.5 (LO)
PHB_FILT: C15.2, D9.3 (K), R16.1, R17.1, TP3.1; also elsewhere on the board
PHB_H: U3.2 (HIN); also elsewhere on the board
PHB_L: U3.3 (LIN); also elsewhere on the board
PHB_MOTOR: C13.1, D7.1 (S), D7.2 (S), D7.3 (S), D8.5 (D), R14.2, R16.2, R18.1, TP4.1, U3.6 (VS); also elsewhere on the board

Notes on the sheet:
RC LOW PASS FILTER, 18.3kHZ
RC SNUBBER
NOTES: AT +VBATT 25.2V, PHASE VOLTAGES DIVIDED DOWN TO 3.23V RC LOW PASS FILTER CUTOFF FREQUENCY AT 18.3kHZ
PHASE B HALF-BRIDGE

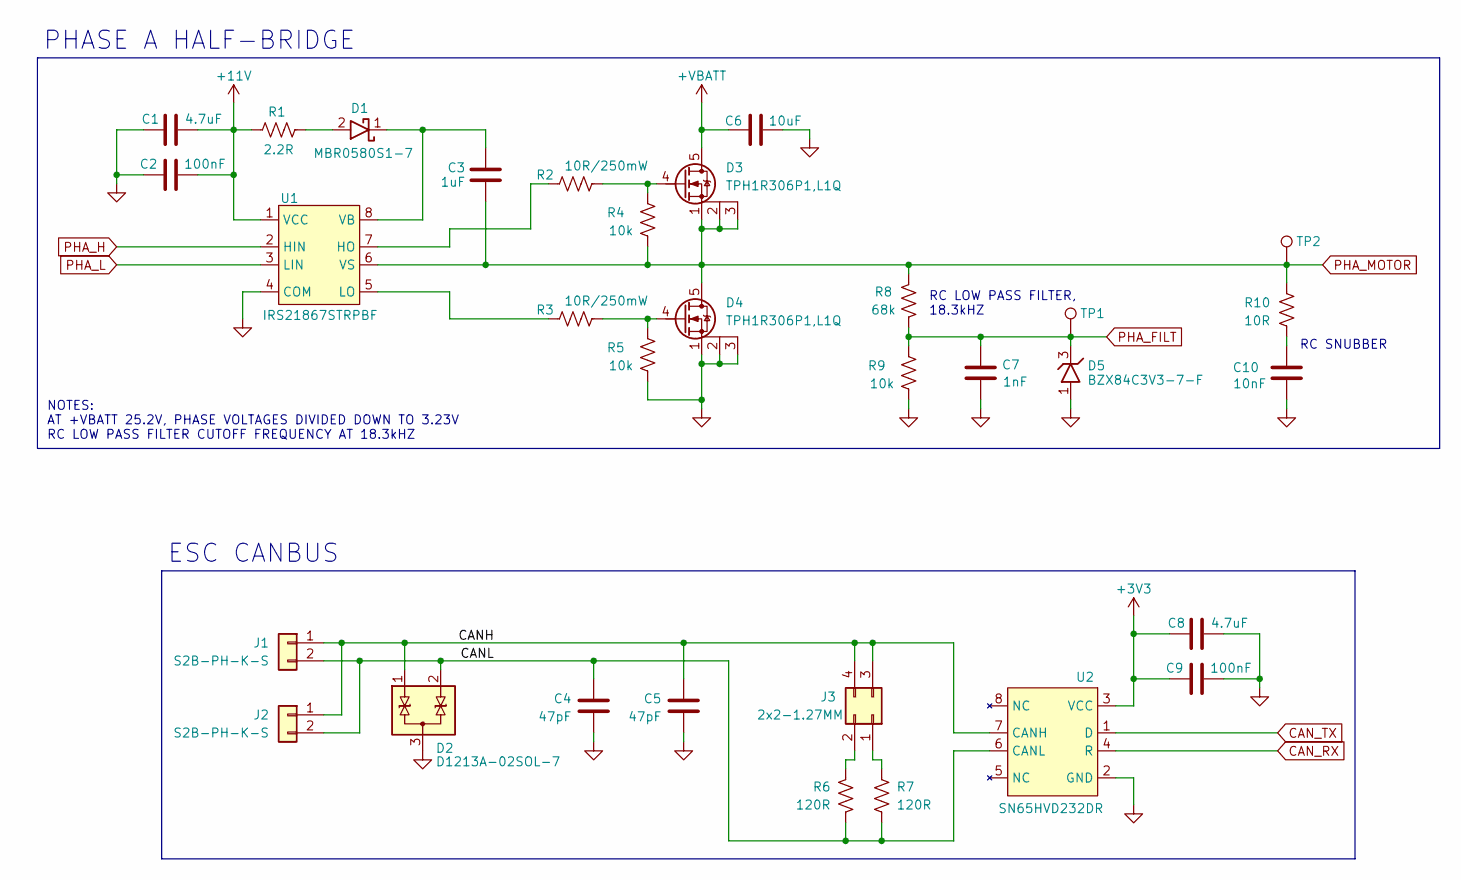
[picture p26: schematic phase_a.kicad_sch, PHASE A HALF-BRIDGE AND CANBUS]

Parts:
C1, C8: 4.7uF; CAP_0805_2012Metric; Manufacturer Part # CL21A475KAQNNNE; JLCPCB Part # C1779
C2, C9: 100nF; CAP_0603_1608Metric; Manufacturer Part # CC0603KRX7R9BB104; JLCPCB Part # C14663
C3: 1uF; CAP_0805_2012Metric; Manufacturer Part # CL21B105KBFNNNE; JLCPCB Part # C28323
C4, C5: 47pF; CAP_0603_1608Metric; Manufacturer Part # CL10C470JB8NNNC; JLCPCB Part # C1671
C6: 10uF; CAP_1206_3216Metric; Manufacturer Part # CL31A106KBHNNNE; JLCPCB Part # C13585
C7: 1nF; CAP_0603_1608Metric; Manufacturer Part # CL10B102KB8NNNC; JLCPCB Part # C1588
C10: 10nF; CAP_0603_1608Metric; Manufacturer Part # CL10B103KB8NNNC; JLCPCB Part # C57112
D1: MBR0580S1-7; DiodesINC_SOD123; Manufacturer Part # MBR0580S1-7; JLCPCB Part # C177047
D2: D1213A-02SOL-7; DiodesINC_SOT23-3; Manufacturer Part # D1213A-02SOL-7; JLCPCB Part # C460585
D3, D4: TPH1R306P1,L1Q; PQFN-8-EP_6x5mm_P1.27mm_Generic; Manufacturer Part # TPH1R306P1,L1Q; JLCPCB Part # C6290261
D5: BZX84C3V3-7-F; DiodesINC_SOT23-3; Manufacturer Part # BZX84C3V3-7-F; JLCPCB Part # C177019
J1, J2: S2B-PH-K-S; CONN_JST_S2B-PH-K-S; Manufacturer Part # S2B-PH-K-S; JLCPCB Part # C173752
J3: 2x2-1.27MM; CONN_MALE_TH_1.27MM_2x2; Manufacturer Part # GRPB022VWVN-RC; JLCPCB Part # C18197867
R1: 2.2R; RES_1206_3216Metric; Manufacturer Part # CRCW12062R20FKEAHP; JLCPCB Part # C1854860
R2, R3: 10R/250mW; RES_0805_2012Metric; Manufacturer Part # AC0805FR-7W10RL; JLCPCB Part # C727983
R4, R5, R9: 10k; RES_0603_1608Metric; Manufacturer Part # RMCF0603FT10K0; JLCPCB Part # C25804
R6, R7: 120R; RES_0603_1608Metric; Manufacturer Part # RC0603FR-07120RL; JLCPCB Part # C22787
R8: 68k; RES_0603_1608Metric; Manufacturer Part # ERJ-3EKF6802V; JLCPCB Part # C23231
R10: 10R; RES_0603_1608Metric; Manufacturer Part # RC0603FR-0710RL; JLCPCB Part # C22859
TP1, TP2: TestPoint; TestPoint_THTPad_D2.5mm_Drill1.2mm
U1: IRS21867STRPBF; SOIC-8; Manufacturer Part # IRS21867STRPBF; JLCPCB Part # C52290
U2: SN65HVD232DR; SOIC-8; Manufacturer Part # SN65HVD232DR; JLCPCB Part # C30530

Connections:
+3V3: C8.1, C9.1, U2.3 (VCC); also elsewhere on the board
+11V: C1.2, C2.2, R1.1, U1.1 (VCC); also elsewhere on the board
+VBATT: C6.1, D3.5 (D); also elsewhere on the board
/PHASE_A/CANH: C5.1, D2.1 (K), J1.1, J2.1, J3.3, J3.4, U2.7 (CANH)
/PHASE_A/CANL: C4.1, D2.2 (K), J1.2, J2.2, R6.2, R7.2, U2.6 (CANL)
CAN_RX: U2.4 (R); also elsewhere on the board
CAN_TX: U2.1 (D); also elsewhere on the board
GND: C1.1, C2.1, C4.2, C5.2, C6.2, C7.1, C8.2, C9.2, C10.1, D2.3 (A), D4.1 (S), D4.2 (S), D4.3 (S), D5.1 (A), R5.2, R9.2, U1.4 (COM), U2.2 (GND); also elsewhere on the board
unnamed: C10.2, R10.2
unnamed: D1.2 (A), R1.2
unnamed: C3.2, D1.1 (K), U1.8 (VB)
unnamed: D3.4 (G), R2.2, R4.1
unnamed: D4.4 (G), R3.2, R5.1
unnamed: J3.1, R7.1
unnamed: J3.2, R6.1
unnamed: R2.1, U1.7 (HO)
unnamed: R3.1, U1.5 (LO)
PHA_FILT: C7.2, D5.3 (K), R8.1, R9.1, TP1.1; also elsewhere on the board
PHA_H: U1.2 (HIN); also elsewhere on the board
PHA_L: U1.3 (LIN); also elsewhere on the board
PHA_MOTOR: C3.1, D3.1 (S), D3.2 (S), D3.3 (S), D4.5 (D), R4.2, R8.2, R10.1, TP2.1, U1.6 (VS); also elsewhere on the board

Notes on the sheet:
RC LOW PASS FILTER, 18.3kHZ
PHASE A HALF-BRIDGE
ESC CANBUS
NOTES: AT +VBATT 25.2V, PHASE VOLTAGES DIVIDED DOWN TO 3.23V RC LOW PASS FILTER CUTOFF FREQUENCY AT 18.3kHZ
RC SNUBBER

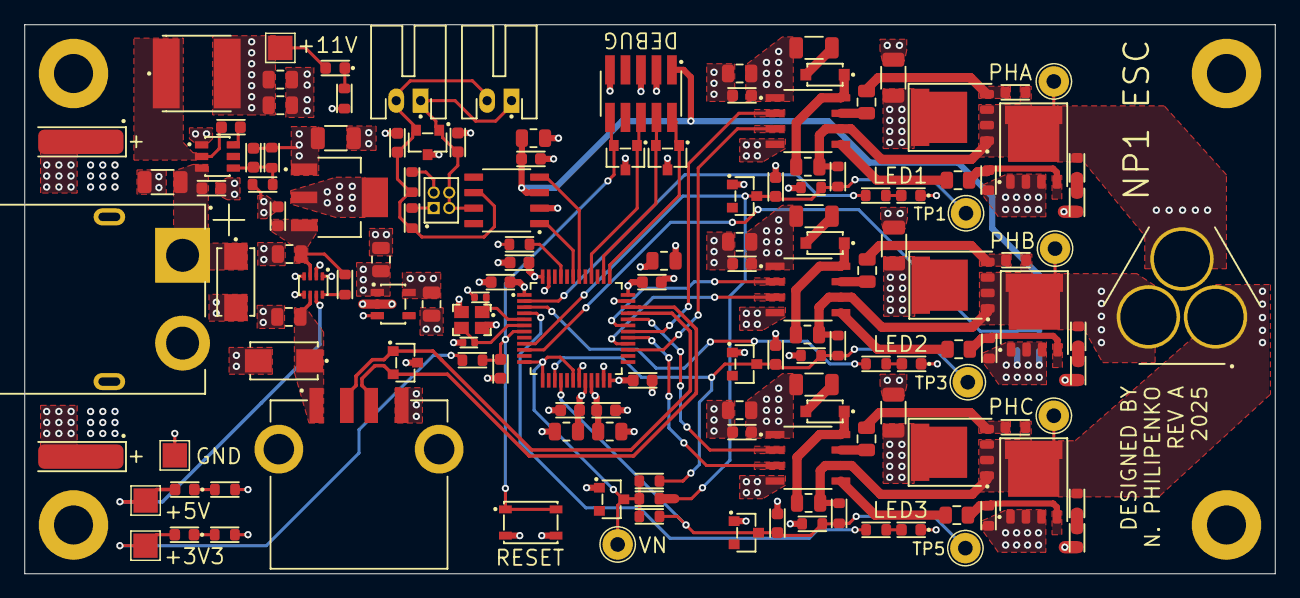
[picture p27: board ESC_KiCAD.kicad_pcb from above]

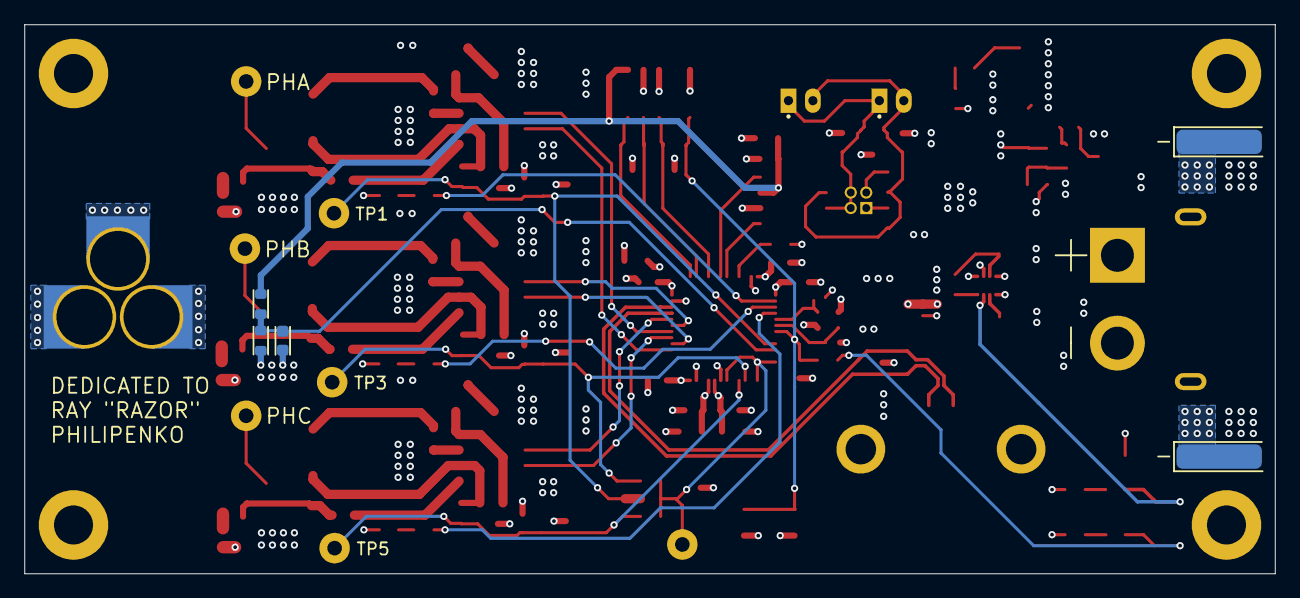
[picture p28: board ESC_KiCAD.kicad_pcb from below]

Board: 4 copper layers, 102.5 x 45.0 mm, 150 parts (3 on the bottom side), 70 nets.

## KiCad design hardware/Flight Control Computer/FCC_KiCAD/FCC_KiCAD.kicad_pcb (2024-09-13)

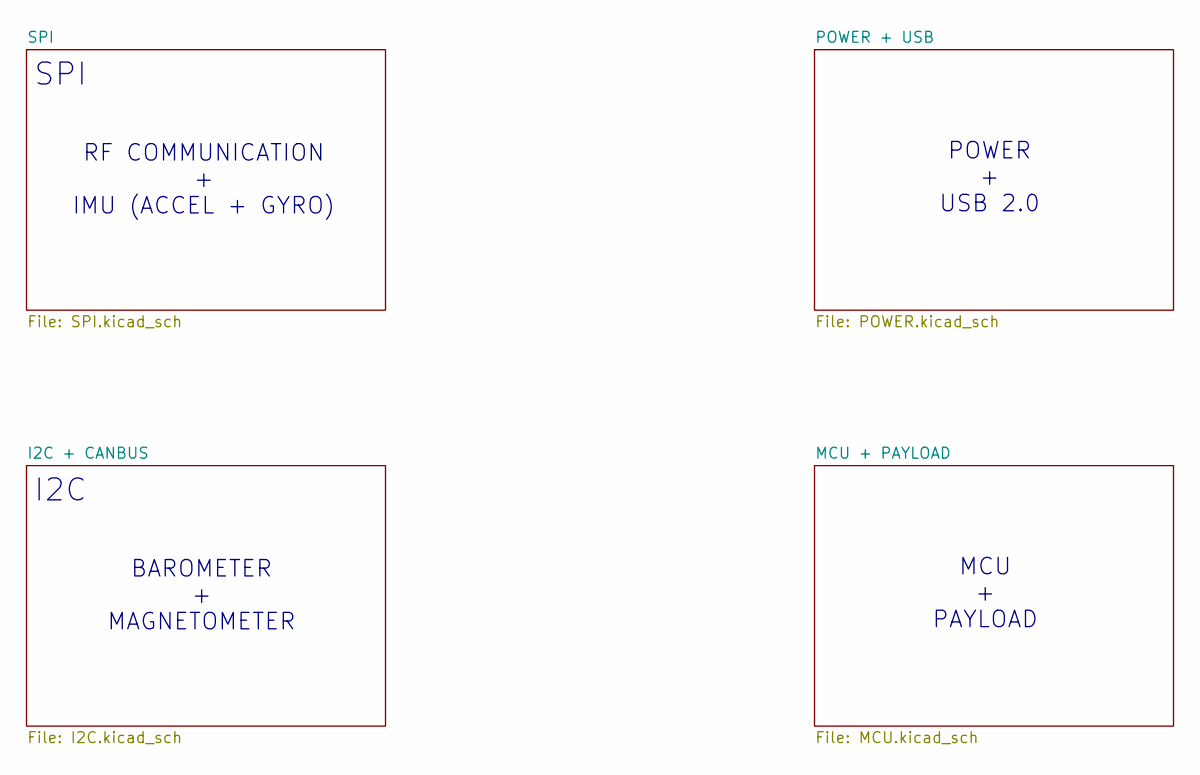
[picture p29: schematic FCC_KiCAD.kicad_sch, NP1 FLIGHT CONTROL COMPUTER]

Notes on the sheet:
MCU + PAYLOAD
BAROMETER + MAGNETOMETER
SPI
POWER + USB 2.0
RF COMMUNICATION + IMU (ACCEL + GYRO)
I2C

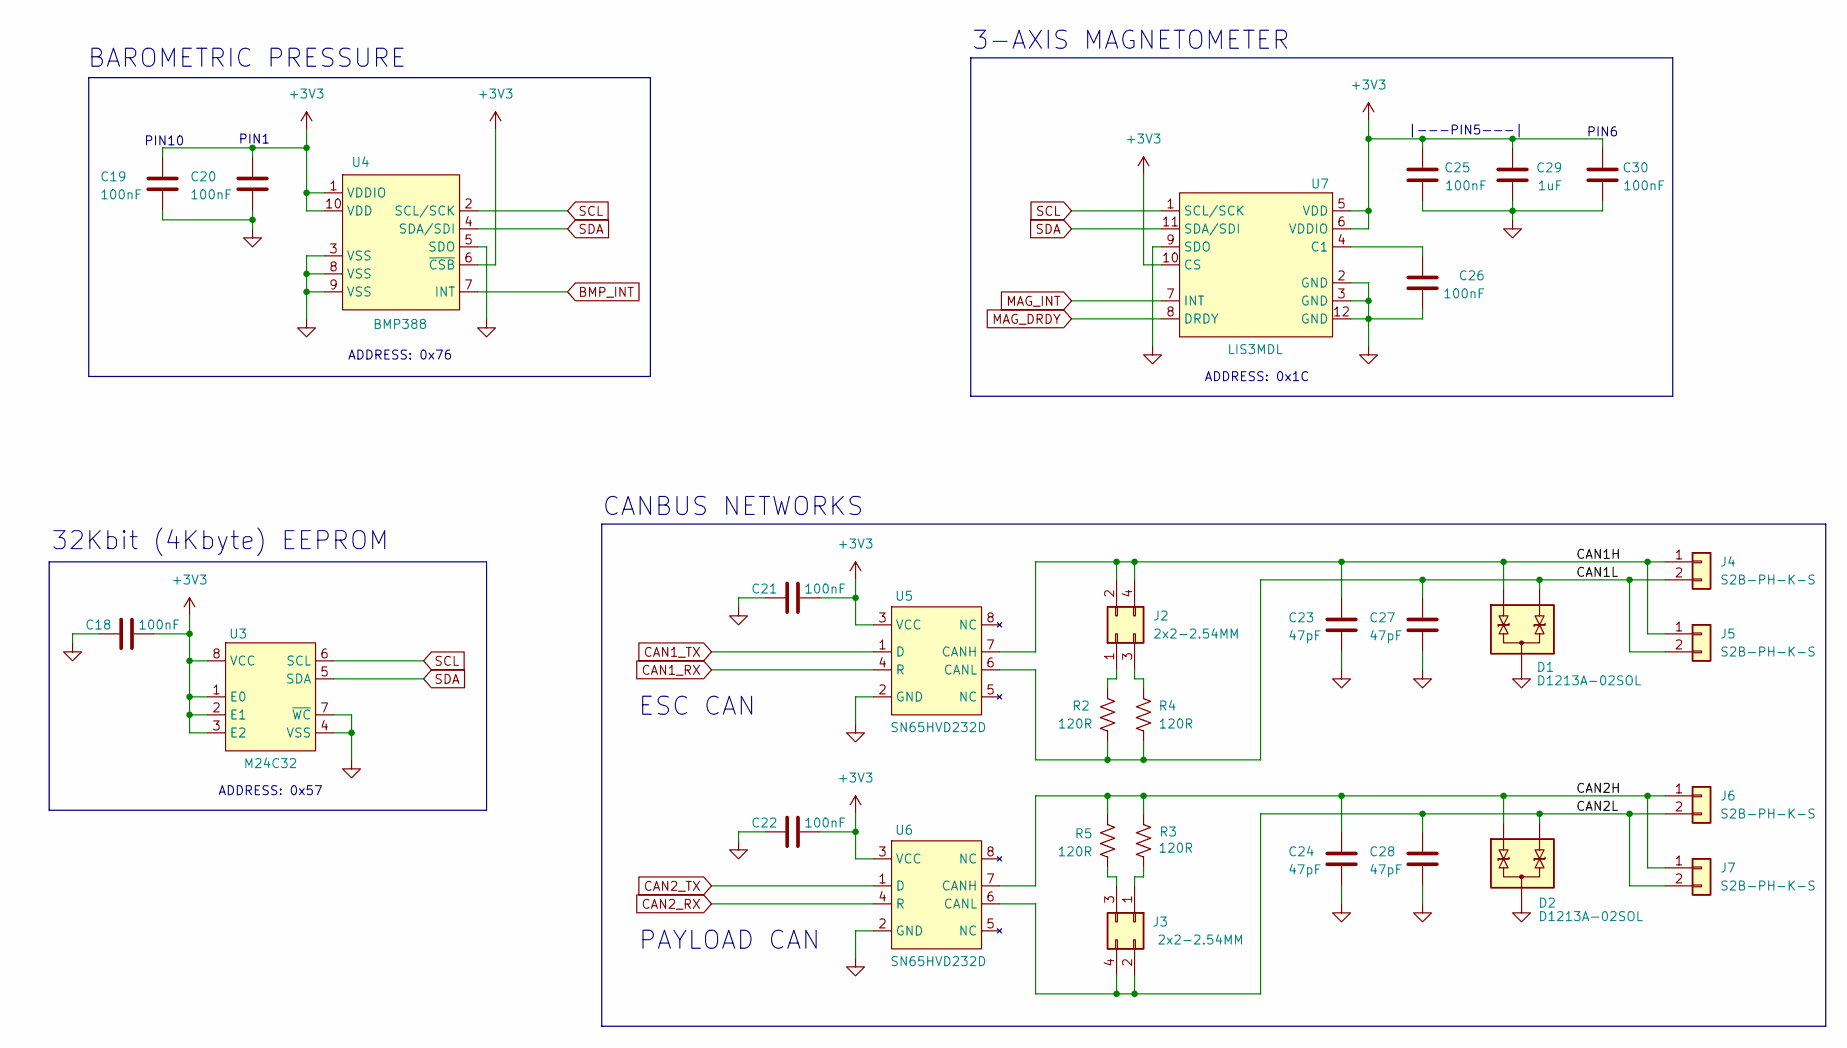
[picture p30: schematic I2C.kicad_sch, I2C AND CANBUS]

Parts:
C18, C19, C20, C21, C22, C25, C26, C30: 100nF; CAP_0402_1005Metric; JLCPCB Part# C77020
C23, C24, C27, C28: 47pF; CAP_0402_1005Metric; JLCPCB Part# C76970
C29: 1uF; CAP_0402_1005Metric; JLCPCB Part# C77009
D1, D2: D1213A-02SOL; DiodesINC_SOT23-3; JLCPCB Part# C460585
J2, J3: 2x2-2.54MM; CONN_MALE_TH_2.54MM_2x2; JLCPCB Part# C66690
J4, J5, J6, J7: S2B-PH-K-S; CONN_JST_S2B-PH-K-S; JLCPCB Part# C173752
R2, R3, R4, R5: 120R; RES_0603_1608Metric; JLCPCB Part# C22787
U3: M24C32; STM_SO8N; JLCPCB Part# C79920
U4: BMP388; BOSCH_LGA-10; JLCPCB Part# C779278
U5, U6: SN65HVD232D; TI_SOIC-8; JLCPCB Part# C30530
U7: LIS3MDL; STM_LGA-12L; JLCPCB Part# C478483

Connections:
+3V3: C18.2, C19.1, C20.1, C21.2, C22.2, C25.1, C29.1, C30.1, U3.1 (E0), U3.2 (E1), U3.3 (E2), U3.8 (VCC), U4.1 (VDDIO), U4.6 (~CSB), U4.10 (VDD), U5.3 (VCC), U6.3 (VCC), U7.5 (VDD), U7.6 (VDDIO), U7.10 (CS); also elsewhere on the board
/I2C + CANBUS/CAN1H: C23.1, D1.1 (K), J2.2, J2.4, J4.1, J5.1, U5.7 (CANH)
/I2C + CANBUS/CAN1L: C27.1, D1.2 (K), J4.2, J5.2, R2.2, R4.2, U5.6 (CANL)
/I2C + CANBUS/CAN2H: C24.1, D2.1 (K), J6.1, J7.1, R3.2, R5.2, U6.7 (CANH)
/I2C + CANBUS/CAN2L: C28.1, D2.2 (K), J3.2, J3.4, J6.2, J7.2, U6.6 (CANL)
BMP_INT: U4.7 (INT); also elsewhere on the board
CAN1_RX: U5.4 (R); also elsewhere on the board
CAN1_TX: U5.1 (D); also elsewhere on the board
CAN2_RX: U6.4 (R); also elsewhere on the board
CAN2_TX: U6.1 (D); also elsewhere on the board
GND: C18.1, C19.2, C20.2, C21.1, C22.1, C23.2, C24.2, C25.2, C26.2, C27.2, C28.2, C29.2, C30.2, D1.3 (A), D2.3 (A), U3.4 (VSS), U3.7 (~WC), U4.3 (VSS), U4.5 (SDO), U4.8 (VSS), U4.9 (VSS), U5.2 (GND), U6.2 (GND), U7.2 (GND), U7.3 (GND), U7.9 (SDO), U7.12 (GND); also elsewhere on the board
MAG_DRDY: U7.8 (DRDY); also elsewhere on the board
MAG_INT: U7.7 (INT); also elsewhere on the board
unnamed: J2.1, R2.1
unnamed: J2.3, R4.1
unnamed: J3.1, R3.1
unnamed: J3.3, R5.1
unnamed: C26.1, U7.4 (C1)
SCL: U3.6 (SCL), U4.2 (SCL/SCK), U7.1 (SCL/SCK); also elsewhere on the board
SDA: U3.5 (SDA), U4.4 (SDA/SDI), U7.11 (SDA/SDI); also elsewhere on the board

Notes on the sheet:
ESC CAN
BAROMETRIC PRESSURE
PIN1
|---PIN5---|
3-AXIS MAGNETOMETER
32Kbit (4Kbyte) EEPROM
CANBUS NETWORKS
PIN10
ADDRESS: 0x76
PAYLOAD CAN
ADDRESS: 0x57
PIN6
ADDRESS: 0x1C

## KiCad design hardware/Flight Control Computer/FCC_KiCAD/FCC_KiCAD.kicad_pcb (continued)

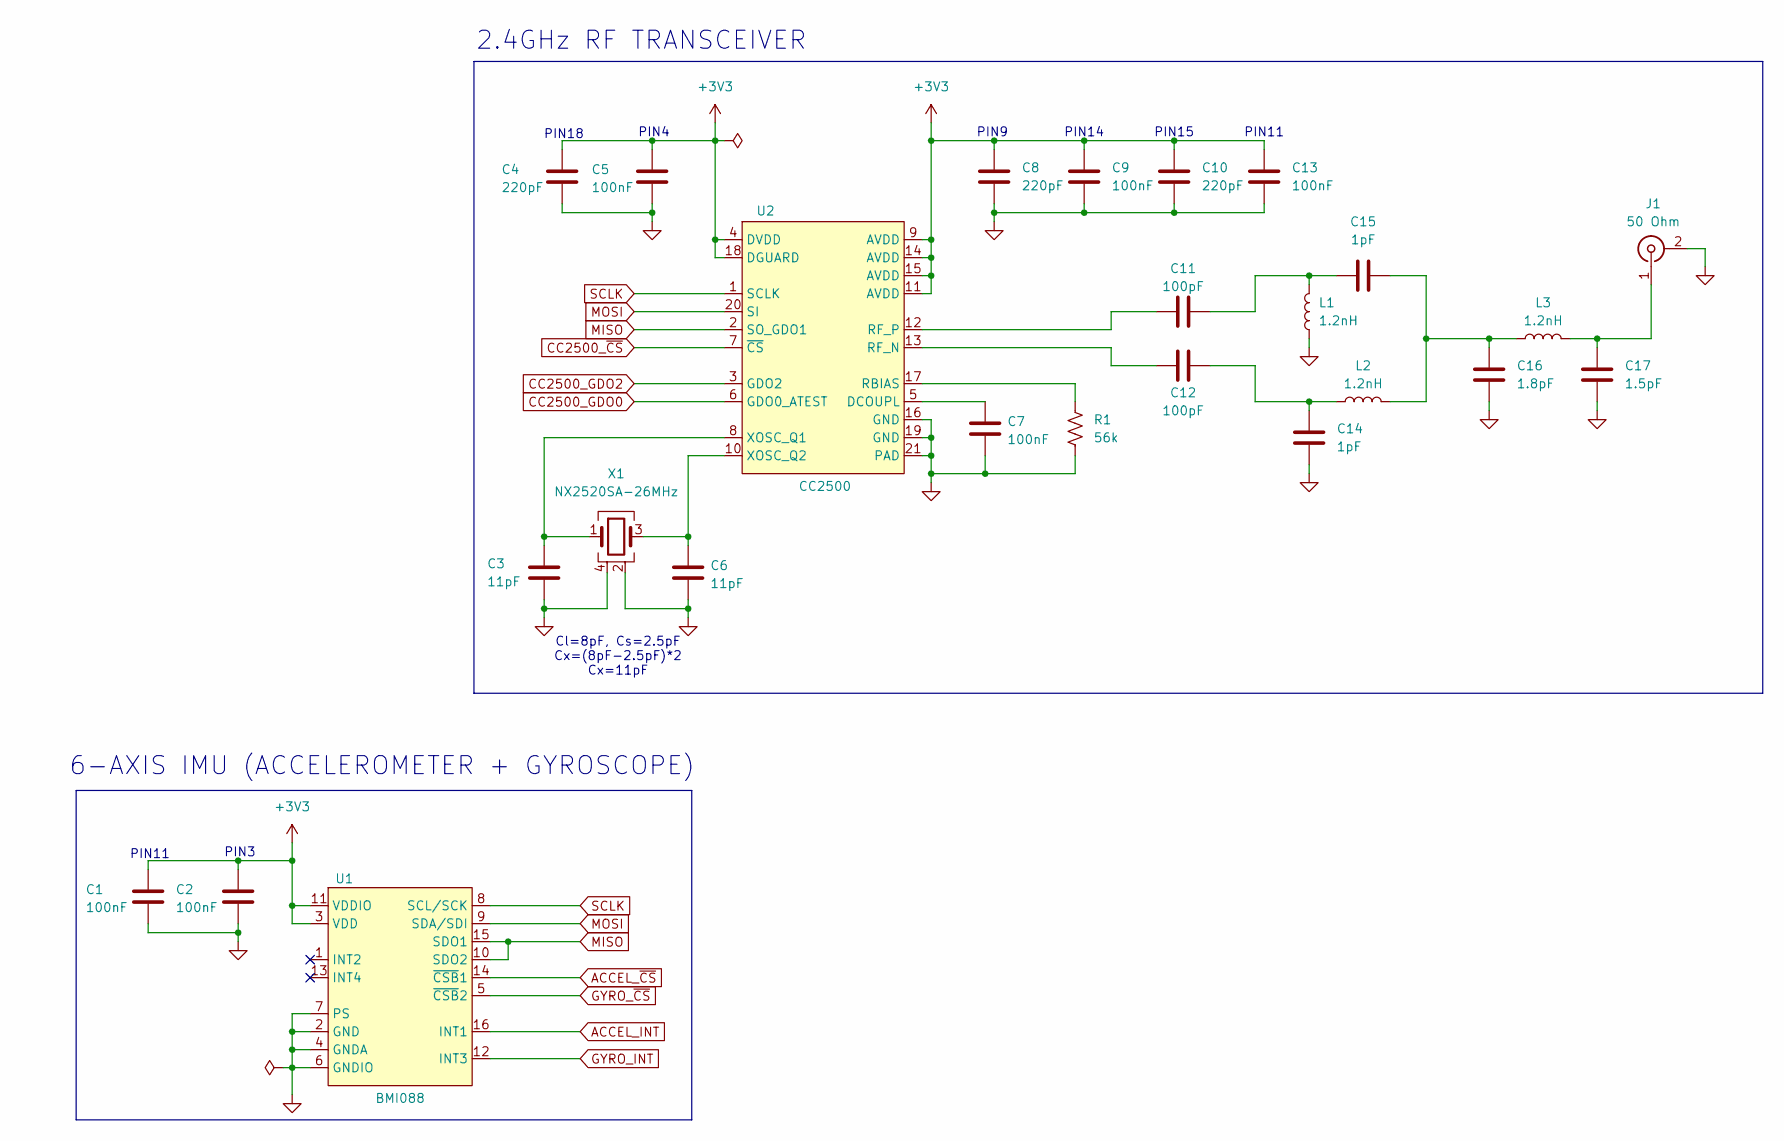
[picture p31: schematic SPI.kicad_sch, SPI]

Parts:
C1, C2, C5, C7, C9, C13: 100nF; CAP_0402_1005Metric; JLCPCB Part# C77020
C3, C6: 11pF; CAP_0402_1005Metric; JLCPCB Part# C710643
C4, C8, C10: 220pF; CAP_0402_1005Metric; JLCPCB Part# C97872
C11, C12: 100pF; CAP_0402_1005Metric; JLCPCB Part# C77177
C14, C15: 1pF; CAP_0402_1005Metric; JLCPCB Part# C76953
C16: 1.8pF; CAP_0402_1005Metric; JLCPCB Part# C85878
C17: 1.5pF; CAP_0402_1005Metric; JLCPCB Part# C76958
J1: 50 Ohm; RF-SMA_Dosinconn_DOSIN-806-0001; JLCPCB Part# C521220
L1, L2, L3: 1.2nH; L_0402_1005Metric; JLCPCB Part# C77105
R1: 56k; RES_0603_1608Metric; JLCPCB Part# C144110
U1: BMI088; BOSCH_LGA-16; JLCPCB Part# C194919
U2: CC2500; TI_QFN-20; JLCPCB Part# C57494
X1: NX2520SA-26MHz; NDK_NX2520SA; JLCPCB Part# C910046

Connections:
+3V3: C1.1, C2.1, C4.1, C5.1, C8.1, C9.1, C10.1, C13.1, U1.3 (VDD), U1.11 (VDDIO), U2.4 (DVDD), U2.9 (AVDD), U2.11 (AVDD), U2.14 (AVDD), U2.15 (AVDD), U2.18 (DGUARD); also elsewhere on the board
ACCEL_INT: U1.16 (INT1); also elsewhere on the board
ACCEL_~CS: U1.14 (~CSB1); also elsewhere on the board
CC2500_GDO0: U2.6 (GDO0_ATEST); also elsewhere on the board
CC2500_GDO2: U2.3 (GDO2); also elsewhere on the board
CC2500_~CS: U2.7 (~CS); also elsewhere on the board
GND: C1.2, C2.2, C3.2, C4.2, C5.2, C6.2, C7.2, C8.2, C9.2, C10.2, C13.2, C14.2, C16.2, C17.2, J1.2 (Ext), L1.1, R1.2, U1.2 (GND), U1.4 (GNDA), U1.6 (GNDIO), U1.7 (PS), U2.16 (GND), U2.19 (GND), U2.21 (PAD), X1.2, X1.4; also elsewhere on the board
GYRO_INT: U1.12 (INT3); also elsewhere on the board
GYRO_~CS: U1.5 (~CSB2); also elsewhere on the board
MISO: U1.10 (SDO2), U1.15 (SDO1), U2.2 (SO_GDO1); also elsewhere on the board
MOSI: U1.9 (SDA/SDI), U2.20 (SI); also elsewhere on the board
unnamed: C11.2, C15.1, L1.2
unnamed: C12.2, C14.1, L2.1
unnamed: C15.2, C16.1, L2.2, L3.1
unnamed: C17.1, J1.1 (In), L3.2
unnamed: C7.1, U2.5 (DCOUPL)
unnamed: R1.1, U2.17 (RBIAS)
unnamed: C12.1, U2.13 (RF_N)
unnamed: C11.1, U2.12 (RF_P)
unnamed: C3.1, U2.8 (XOSC_Q1), X1.1
unnamed: C6.1, U2.10 (XOSC_Q2), X1.3
SCLK: U1.8 (SCL/SCK), U2.1 (SCLK); also elsewhere on the board

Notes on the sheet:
2.4GHz RF TRANSCEIVER
PIN11
PIN4
PIN18
PIN14
6-AXIS IMU (ACCELEROMETER + GYROSCOPE)
PIN9
PIN3
Cl=8pF, Cs=2.5pF Cx=(8pF-2.5pF)*2 Cx=11pF
PIN15

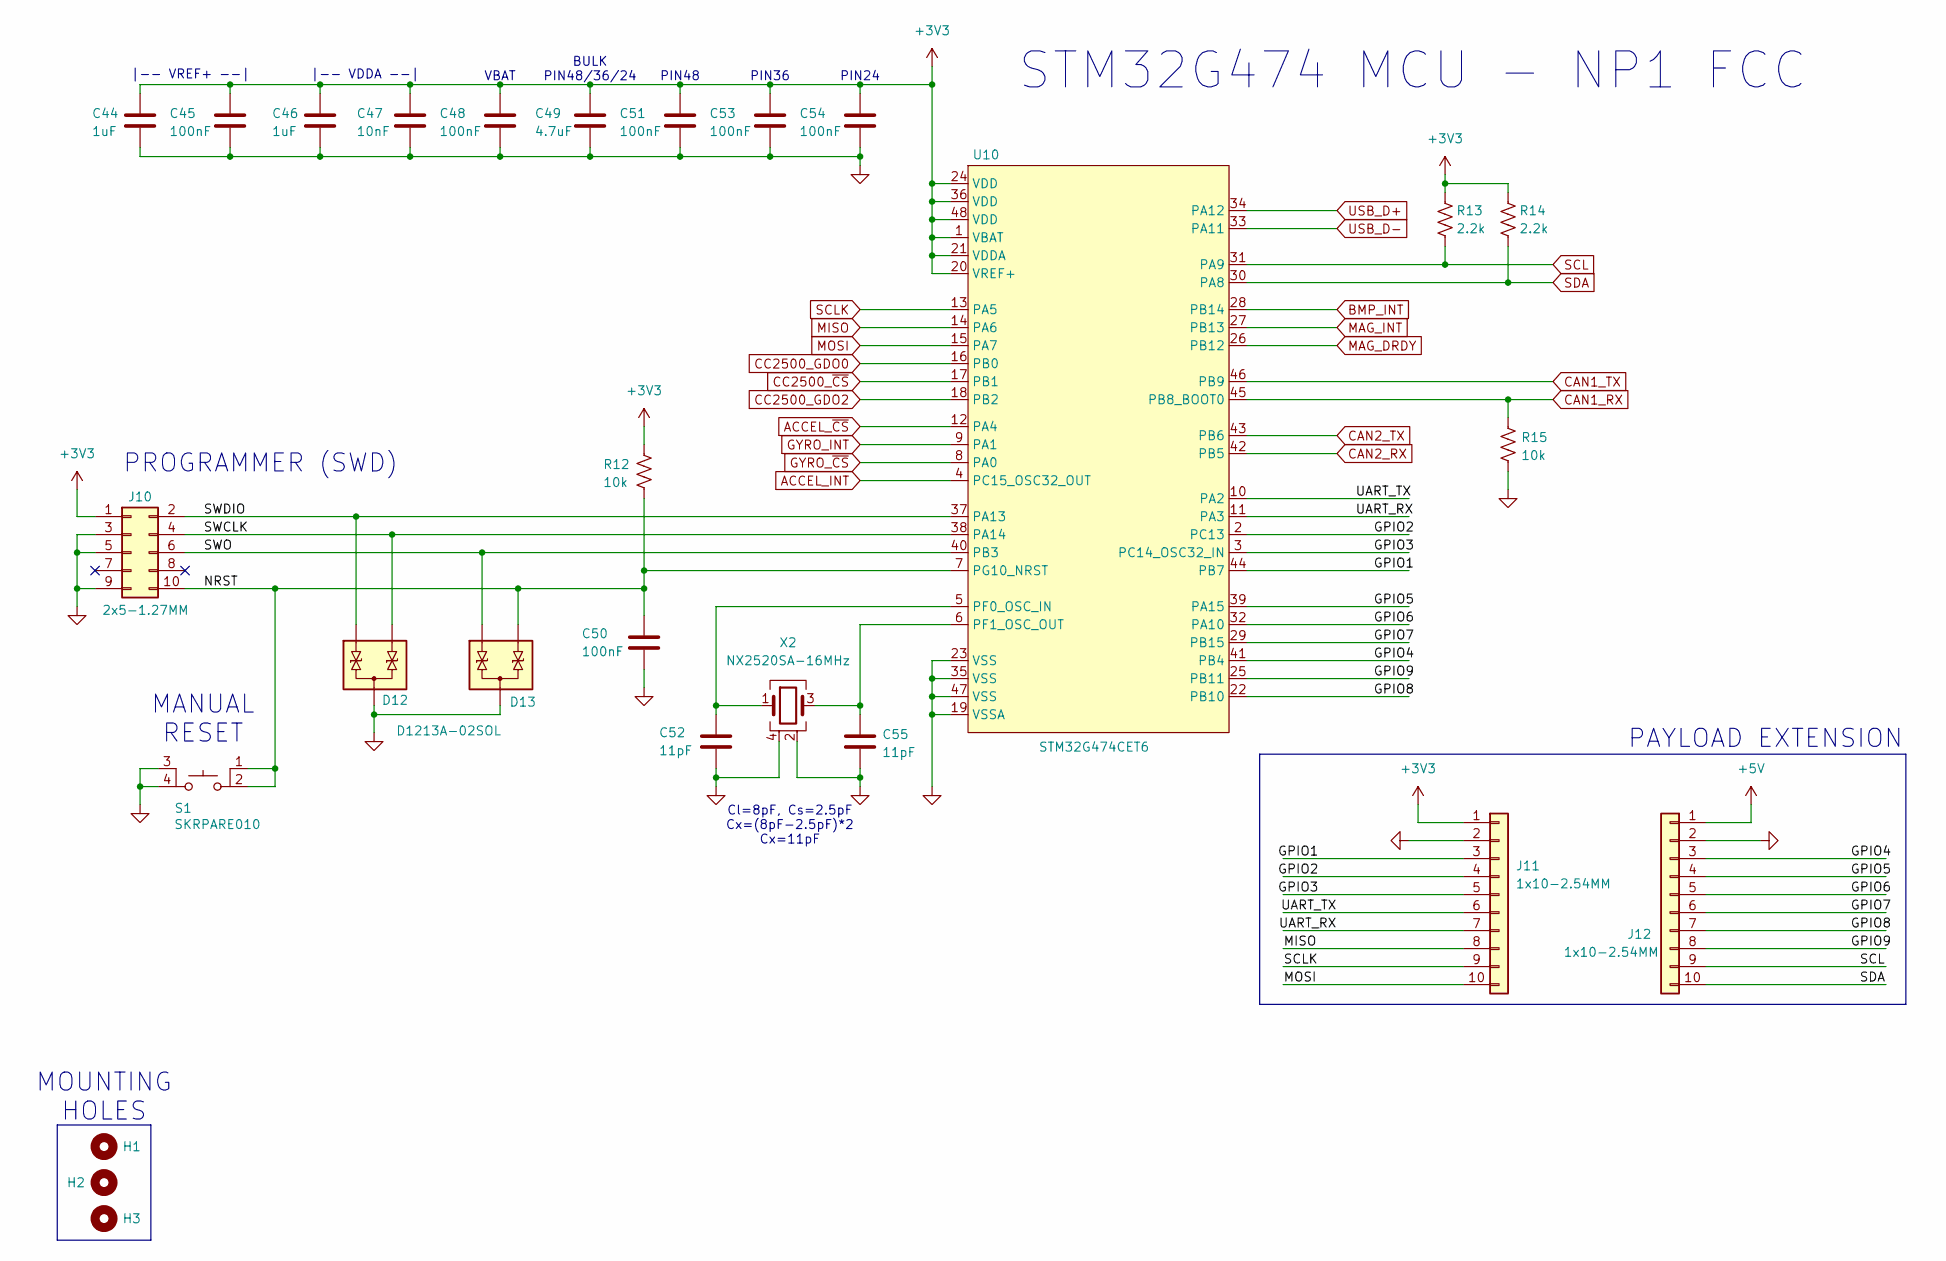
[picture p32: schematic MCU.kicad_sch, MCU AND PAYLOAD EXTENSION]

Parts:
C44, C46: 1uF; CAP_0402_1005Metric; JLCPCB Part# C77009
C45, C48, C50, C51, C53, C54: 100nF; CAP_0402_1005Metric; JLCPCB Part# C77020
C47: 10nF; CAP_0402_1005Metric; JLCPCB Part# C162190
C49: 4.7uF; CAP_0402_1005Metric; JLCPCB Part# C77004
C52, C55: 11pF; CAP_0402_1005Metric; JLCPCB Part# C710643
D12, D13: D1213A-02SOL; DiodesINC_SOT23-3; JLCPCB Part# C460585
H1, H2, H3: MountingHole; MountingHole_2.2mm_M2_Pad
J10: 2x5-1.27MM; CONN_MALE_SMT_1.27MM_2x5; JLCPCB Part# C150517
J11, J12: 1x10-2.54MM; CONN_FEMALE_TH_2.54MM_1x10; JLCPCB Part# C2897373
R12, R15: 10k; RES_0603_1608Metric; JLCPCB Part# C98220
R13, R14: 2.2k; RES_0603_1608Metric; JLCPCB Part# C114662
S1: SKRPARE010; TACT_SKRP; JLCPCB Part# C341730
U10: STM32G474CET6; STM_LQFP48; JLCPCB Part# C730125
X2: NX2520SA-16MHz; NDK_NX2520SA; JLCPCB Part# C280836

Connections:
+3V3: C44.1, C45.1, C46.1, C47.1, C48.1, C49.1, C51.1, C53.1, C54.1, J10.1, J11.1, R12.1, R13.1, R14.1, U10.1 (VBAT), U10.20 (VREF+), U10.21 (VDDA), U10.24 (VDD), U10.36 (VDD), U10.48 (VDD); also elsewhere on the board
+5V: J12.1; also elsewhere on the board
/MCU + PAYLOAD/GPIO1: J11.3, U10.44 (PB7)
/MCU + PAYLOAD/GPIO2: J11.4, U10.2 (PC13)
/MCU + PAYLOAD/GPIO3: J11.5, U10.3 (PC14_OSC32_IN)
/MCU + PAYLOAD/GPIO4: J12.3, U10.41 (PB4)
/MCU + PAYLOAD/GPIO5: J12.4, U10.39 (PA15)
/MCU + PAYLOAD/GPIO6: J12.5, U10.32 (PA10)
/MCU + PAYLOAD/GPIO7: J12.6, U10.29 (PB15)
/MCU + PAYLOAD/GPIO8: J12.7, U10.22 (PB10)
/MCU + PAYLOAD/GPIO9: J12.8, U10.25 (PB11)
/MCU + PAYLOAD/NRST: C50.1, D13.2 (K), J10.10, R12.2, S1.1, S1.2, U10.7 (PG10_NRST)
/MCU + PAYLOAD/SWCLK: D12.2 (K), J10.4, U10.38 (PA14)
/MCU + PAYLOAD/SWDIO: D12.1 (K), J10.2, U10.37 (PA13)
/MCU + PAYLOAD/SWO: D13.1 (K), J10.6, U10.40 (PB3)
/MCU + PAYLOAD/UART_RX: J11.7, U10.11 (PA3)
/MCU + PAYLOAD/UART_TX: J11.6, U10.10 (PA2)
ACCEL_INT: U10.4 (PC15_OSC32_OUT); also elsewhere on the board
ACCEL_~CS: U10.12 (PA4); also elsewhere on the board
BMP_INT: U10.28 (PB14); also elsewhere on the board
CAN1_RX: R15.1, U10.45 (PB8_BOOT0); also elsewhere on the board
CAN1_TX: U10.46 (PB9); also elsewhere on the board
CAN2_RX: U10.42 (PB5); also elsewhere on the board
CAN2_TX: U10.43 (PB6); also elsewhere on the board
CC2500_GDO0: U10.16 (PB0); also elsewhere on the board
CC2500_GDO2: U10.18 (PB2); also elsewhere on the board
CC2500_~CS: U10.17 (PB1); also elsewhere on the board
GND: C44.2, C45.2, C46.2, C47.2, C48.2, C49.2, C50.2, C51.2, C52.2, C53.2, C54.2, C55.2, D12.3 (A), D13.3 (A), J10.3, J10.5, J10.9, J11.2, J12.2, R15.2, S1.3, S1.4, U10.19 (VSSA), U10.23 (VSS), U10.35 (VSS), U10.47 (VSS), X2.2, X2.4; also elsewhere on the board
GYRO_INT: U10.9 (PA1); also elsewhere on the board
GYRO_~CS: U10.8 (PA0); also elsewhere on the board
MAG_DRDY: U10.26 (PB12); also elsewhere on the board
MAG_INT: U10.27 (PB13); also elsewhere on the board
MISO: J11.8, U10.14 (PA6); also elsewhere on the board
MOSI: J11.10, U10.15 (PA7); also elsewhere on the board
unnamed: C52.1, U10.5 (PF0_OSC_IN), X2.1
unnamed: C55.1, U10.6 (PF1_OSC_OUT), X2.3
SCL: J12.9, R13.2, U10.31 (PA9); also elsewhere on the board
SCLK: J11.9, U10.13 (PA5); also elsewhere on the board
SDA: J12.10, R14.2, U10.30 (PA8); also elsewhere on the board
USB_D+: U10.34 (PA12); also elsewhere on the board
USB_D-: U10.33 (PA11); also elsewhere on the board

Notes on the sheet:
PAYLOAD EXTENSION
STM32G474 MCU - NP1 FCC
MOUNTING HOLES
PIN48
VBAT
|-- VREF+ --|
|-- VDDA --|
PROGRAMMER (SWD)
Cl=8pF, Cs=2.5pF Cx=(8pF-2.5pF)*2 Cx=11pF
PIN24
BULK PIN48/36/24
MANUAL RESET
PIN36


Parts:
C31, C36: 150uF; NICHICON_UHE_10x12.5; JLCPCB Part# C116230
C32, C33, C42: 10nF; CAP_0402_1005Metric; JLCPCB Part# C162190
C34: 100nF; CAP_0402_1005Metric; JLCPCB Part# C77020
C35: 6.8uF; CAP_0603_1608Metric; JLCPCB Part# C338096
C37, C38, C39, C40, C43: 1uF; CAP_0402_1005Metric; JLCPCB Part# C77009
C41: 2.2uF; CAP_0402_1005Metric; JLCPCB Part# C385032
D3: SMAJ45A; DiodesINC_SMA; JLCPCB Part# C134989
D4: SMAJ5.0A; DiodesINC_SMA; JLCPCB Part# C87074
D5: D1213A-02SOL; DiodesINC_SOT23-3; JLCPCB Part# C460585
D6: B150; DiodesINC_SMA; JLCPCB Part# C134431
D7, D9: MAX40200AUK; AnalogDevices_SOT23-5; JLCPCB Part# C2649430
D8: DMN65D8L; DiodesINC_SOT23-3; JLCPCB Part# C155341
D10, D11: LED; LED_0603_1608Metric; JLCPCB Part# C72038
FB1: 330R; L_0603_1608Metric; JLCPCB Part# C710391
J8: XT60; CONN_MALE_TH_XT60; JLCPCB Part# C98733
J9: USB TYPE-A; USB2.0_4P_AMPHENOL_87583-2010BLF; JLCPCB Part# C599118
L4: 47uH; TDK_CLF7045-D; JLCPCB Part# C432960
R6, R11: 0R5; RES_0603_1608Metric; JLCPCB Part# C309622
R7, R9: 10k; RES_0603_1608Metric; JLCPCB Part# C98220
R8: 100k; RES_0603_1608Metric; JLCPCB Part# C14675
R10: 1k; RES_0603_1608Metric; JLCPCB Part# C22548
U8: LM2672; TI_SOIC-8; JLCPCB Part# C180371
U9: TPS79633; TI_SOT223-6; JLCPCB Part# C485803

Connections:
+3V3: C43.2, R11.1, U9.4 (OUT); also elsewhere on the board
+5V: C39.2, C40.2, C41.1, D7.5 (OUT), D9.5 (OUT), R10.1, U9.1 (EN), U9.2 (IN); also elsewhere on the board
+BATT: C31.1, D3.1 (K), J8.1, U8.7 (VIN)
/POWER + USB/5VBUS: C32.2, D4.1 (K), FB1.1, J9.1 (VBUS)
/POWER + USB/5VBUS_FILT: C34.2, C35.2, C38.2, D9.1 (VDD), FB1.2, R9.1
/POWER + USB/5VDCDC: C36.1, C37.2, D7.1 (VDD), L4.2, R7.1, U8.4 (FB)
GND: C31.2, C32.1, C34.1, C36.2, C37.1, C38.1, C39.1, C40.1, C41.2, C42.1, C43.1, D3.2 (A), D4.2 (A), D5.3 (A), D6.2 (A), D7.2 (GND), D8.2 (S), D9.2 (GND), D10.1 (K), D11.1 (K), J8.2, J9.4 (GND), R6.2, R8.2, U8.6 (GND), U9.3 (GND), U9.6 (GND); also elsewhere on the board
unnamed: C35.1, R6.1
unnamed: C33.2, D6.1 (K), L4.1, U8.8 (VSW)
unnamed: D7.3 (EN), D8.1 (G), R7.2, R8.1
unnamed: D8.3 (D), D9.3 (EN), R9.2
unnamed: D10.2 (A), R10.2
unnamed: D11.2 (A), R11.2
unnamed: C33.1, U8.1 (CB)
unnamed: C42.2, U9.5 (NR/FB)
USB_D+: D5.2 (K), J9.3 (D+); also elsewhere on the board
USB_D-: D5.1 (K), J9.2 (D-); also elsewhere on the board

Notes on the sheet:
MAIN USB | OUT ----------------------- 0V 0V 0V 5V 0V MAIN 5V 0V 5V USB 5V 5V 5V MAIN 5V
POWER STATUS LEDS
USB DEVICE, LEAVE SHIELD OPEN, HOST RESPONSIBLE FOR GROUNDING
USB2.0 TYPE-A: POWER AND DATA
USB
+5V POWER SWITCH
HIGH PSRR RF LDO
R6 ACTS AS A DAMPER FOR LC RESONANT FREQUENCIES
+5V POWER TRUTH TABLE
STEP-DOWN DC-DC REGULATOR
SEE LM2672 DATASHEET FOR COMPONENT DERATING
MAIN
+BATT 6V5 TO 40V INPUT 1A MAX LOAD CURRENT
OUT


Board: 4 copper layers, 55.3 x 70.2 mm, 116 parts (0 on the bottom side), 72 nets.

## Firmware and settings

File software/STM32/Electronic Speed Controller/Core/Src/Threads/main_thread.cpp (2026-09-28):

/*
 * main_thread.cpp
 *
 *  Created on: Jun 2, 2026
 *      Author: Nikolai Philipenko
 */

#include "main.h"
#include "fdcan.h"
#include "comp.h"

#include "Threads/main_thread.hpp"
#include "Threads/main_thread_types.hpp"
#include "Drivers/commutator.hpp"
#include "Canbus/can_message.hpp"
#include "constants.hpp"

/*
 *
 * PROTOTYPES
 *
 */
void handle_standby_state(EscState& current_state, ThreadInput& input, Commutator& comm);
void handle_arming_state(EscState& current_state, ThreadInput& input, Commutator& comm);
void handle_armed_state(EscState& current_state, ThreadInput& input, Commutator& comm);

void Delay_us(uint32_t us);

/*
 *
 * GLOBAL
 *
 */
FDCAN_RxHeaderTypeDef rx_header;
uint8_t rx_data[CAN_BUFFER_SIZE];

const int MIN_ARMED_SPEED_PERC		= 25;

const int ESC_ID					= 0;	// 0-3

/*
 *
 * THREADS
 *
 */
void main_thread()
{
	Commutator comm{};
	EscState current_state = EscState::StandBy;

	// ESC heartbeat (receive)
	const unsigned esc_heartbeat_tick_delta = osKernelGetTickFreq() / constants::REQUIRED_ESC_HEARTBEAT_HZ * constants::HEARTBEAT_RX_TOLERANCE_MULTIPLIER;
	unsigned esc_last_heartbeat_tick_count = 0;

	/*
	 * RUN ESC STATE MACHINE
	 */
	while(1)
	{
		// Try semantics
		ThreadInput input{ InputType_None };
		osMessageQueueGet(threadInputQueueHandle, &input, NULL, 0);

		// Check FCC heartbeat

		if (input.type == InputType_CanHeartbeat)
		{
			esc_last_heartbeat_tick_count = osKernelGetTickCount();
		}
		if (osKernelGetTickCount() - esc_last_heartbeat_tick_count > esc_heartbeat_tick_delta)
		{
			ThreadInput input{ InputType_CanDisarm };
			osMessageQueuePut(threadInputQueueHandle, &input, 0, 0);
		}

		// State machine

		switch (current_state)
		{
			case EscState::StandBy: {
				handle_standby_state(current_state, input, comm);
				break;
			}
			case EscState::Arming: {
				handle_arming_state(current_state, input, comm);
				break;
			}
			case EscState::Armed: {
				handle_armed_state(current_state, input, comm);
				break;
			}
		}
	}
}

/*
 *
 * STATE FUNCTIONS
 *
 */
void handle_standby_state(EscState& current_state, ThreadInput& input, Commutator& comm)
{
	// Handle input
	if (input.type == InputType_CanArm)
	{
		current_state = EscState::Arming;
		return;
	}

	// Responsibility
	comm.set_speed_percent(0);
}

void handle_arming_state(EscState& current_state, ThreadInput& input, Commutator& comm)
{
	// ALIGN step tuning parameters
	const float align_time_seconds = 0.8;
	const unsigned align_ticks_delta = osKernelGetTickFreq() * align_time_seconds;

	// OPEN-LOOP Ramp up tuning parameters
	const int start_delay_us 	= 5000;
	const int target_delay_us 	= 100;
	const int start_speed_perc 	= 5;
	const int target_speed_perc	= MIN_ARMED_SPEED_PERC;
	const int ramp_step			= 50;

	// Static function parameters
	static bool align_init = false;
	static int align_ticks_begin = 0;
	static int current_delay = start_delay_us;
	static int current_speed = start_speed_perc;

	// Handle input
	if (input.type == InputType_CanDisarm || input.type == InputType_ArmingComplete)
	{
		// Reset static variables for next ARMING sequence
		align_init = false;
		align_ticks_begin = 0;
		current_delay = start_delay_us;
		current_speed = start_speed_perc;

		if (input.type == InputType_CanDisarm)
		{
			current_state = EscState::StandBy;
			return;
		}
		else if (input.type == InputType_ArmingComplete)
		{
			comm.enable_bldc_step_closed_loop();
			current_state = EscState::Armed;
			return;
		}
	}

	// Responsibility

	// ALIGN step

	if(!align_init)
	{
		comm.set_speed_percent(start_speed_perc);
		comm.bldc_step_open_loop();
		align_init = true;
		align_ticks_begin = osKernelGetTickCount();
	}

	if(osKernelGetTickCount() - align_ticks_begin > align_ticks_delta)
	{
		// OPEN-LOOP Ramp up step

		// current_speed goes from low to high
		// current_delay goes from high to low

		// both interpolate linearly between their bounds

		if(current_delay > target_delay_us)
		{
			comm.set_speed_percent(current_speed);
			comm.bldc_step_open_loop();

			Delay_us(current_delay);

			// Decrease delay (increase frequency) with ramp step
			current_delay -= ramp_step;

			// Linear interpolation with delay to increase speed
			current_speed = start_speed_perc + (float)(current_delay - start_delay_us) * (target_speed_perc - start_speed_perc) / (target_delay_us - start_delay_us);
		}
		else
		{
			ThreadInput input{ InputType_ArmingComplete };
			osMessageQueuePut(threadInputQueueHandle, &input, 0, 0);
		}
	}
}

void handle_armed_state(EscState& current_state, ThreadInput& input, Commutator& comm)
{
	// Handle input
	if (input.type == InputType_CanDisarm)
	{
		comm.disable_bldc_step_closed_loop();
		current_state = EscState::StandBy;
		return;
	}

	// CLOSED-LOOP BLDC control

	else if (input.type == InputType_IsrBemfPoll)
	{
		comm.bldc_step_closed_loop();
	}
	else if (input.type == InputType_CanSpeed)
	{
		// BIG ENDIAN
		uint16_t raw_speed_int = static_cast<uint16_t>(input.payload[0] << 8) | static_cast<uint16_t>(input.payload[1]);
		float raw_speed_frac = static_cast<float>(raw_speed_int) / UINT16_MAX;

		// raw speed 0% -> min allowed armed speed
		// raw speed 100% -> max speed

		float applied_speed_perc = (100.0 - MIN_ARMED_SPEED_PERC) * raw_speed_frac + MIN_ARMED_SPEED_PERC;

		comm.set_speed_percent(applied_speed_perc);
	}
}

void Delay_us (uint32_t us)
{
	// Reset the counter value
	TIM2->CNT = 0;

	// Perform wait
	while (TIM2->CNT < us);
}

/*
 *
 * CALLBACKS
 *
 */
void HAL_TIM_PWM_PulseFinishedCallback(TIM_HandleTypeDef *htim)
{
	if (htim->Instance == TIM1)
	{
		ThreadInput input{ InputType_IsrBemfPoll };
		osMessageQueuePut(threadInputQueueHandle, &input, 0, 0);
	}
}

void HAL_FDCAN_RxFifo0Callback(FDCAN_HandleTypeDef *hfdcan, uint32_t RxFifo0ITs)
{
	if (hfdcan->Instance == FDCAN2)
	{
		if ((RxFifo0ITs & FDCAN_IT_RX_FIFO0_NEW_MESSAGE) != 0)
		{
		    // Retrieve Rx message from RX FIFO0
		    if (HAL_FDCAN_GetRxMessage(hfdcan, FDCAN_RX_FIFO0, &rx_header, rx_data) != HAL_OK)
		    {
		    	return;
//		    	Error_Handler();	// Do not want to just die
		    }

		    switch (static_cast<CanbusMsgID>(rx_header.Identifier))
		    {
				case CanbusMsgID::Disarm: {
					ThreadInput input{ InputType_CanDisarm };
					osMessageQueuePut(threadInputQueueHandle, &input, 0, 0);
					break;
				}
				case CanbusMsgID::Arm: {
					ThreadInput input{ InputType_CanArm };
					osMessageQueuePut(threadInputQueueHandle, &input, 0, 0);
					break;
				}
				case CanbusMsgID::Speed: {
					ThreadInput input { InputType_CanSpeed };
					input.payload[0] = rx_data[ESC_ID * 2];
					input.payload[1] = rx_data[(ESC_ID + 1) * 2 - 1];
					osMessageQueuePut(threadInputQueueHandle, &input, 0, 0);
					break;
				}
				case CanbusMsgID::Heartbeat: {
					ThreadInput input{ InputType_CanHeartbeat };
					osMessageQueuePut(threadInputQueueHandle, &input, 0, 0);
					break;
				}
		    }
		}
	}
}

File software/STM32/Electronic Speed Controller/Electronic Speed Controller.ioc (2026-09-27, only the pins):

Mcu.UserName=STM32G474CETx
PA1.GPIO_Label=PHA_FILT
PA1.Signal=COMP1_INP
PA10.GPIO_Label=PHC_H
PA10.Signal=S_TIM1_CH3
PA11.Signal=USB_DM
PA12.Signal=USB_DP
PA13.Signal=SYS_JTMS-SWDIO
PA14.Signal=SYS_JTCK-SWCLK
PA2.GPIO_Label=TEMP
PA2.Signal=ADC1_IN3
PA4.GPIO_Label=PH_VNA
PA4.Signal=COMP1_INM
PA5.GPIO_Label=PH_VNB
PA5.Signal=COMP2_INM
PA7.GPIO_Label=PHB_FILT
PA7.Signal=COMP2_INP
PA8.GPIO_Label=PHA_H
PA8.Signal=S_TIM1_CH1
PA9.GPIO_Label=PHB_H
PA9.Signal=S_TIM1_CH2
PB0.GPIO_Label=PHC_FILT
PB0.Signal=COMP4_INP
PB13.GPIO_Label=PHA_L
PB13.Signal=TIM1_CH1N
PB14.GPIO_Label=PHB_L
PB14.Signal=TIM1_CH2N
PB15.GPIO_Label=PHC_L
PB15.Signal=TIM1_CH3N
PB2.GPIO_Label=PH_VNC
PB2.Signal=COMP4_INM
PB3.Signal=SYS_JTDO-SWO
PB5.Signal=FDCAN2_RX
PB6.Signal=FDCAN2_TX
PC13.GPIO_Label=LED1
PC13.Signal=GPIO_Output
PC14-OSC32_IN.GPIO_Label=LED2
PC14-OSC32_IN.Signal=GPIO_Output
PC15-OSC32_OUT.GPIO_Label=LED3
PC15-OSC32_OUT.Signal=GPIO_Output
PF0-OSC_IN.Signal=RCC_OSC_IN
PF1-OSC_OUT.Signal=RCC_OSC_OUT

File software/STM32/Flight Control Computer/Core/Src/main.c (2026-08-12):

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
/* Includes ------------------------------------------------------------------*/
#include "main.h"
#include "cmsis_os.h"
#include "crc.h"
#include "dma.h"
#include "fdcan.h"
#include "i2c.h"
#include "spi.h"
#include "tim.h"
#include "usart.h"
#include "usb_device.h"
#include "gpio.h"


/* USER CODE BEGIN PV */
volatile unsigned long ulHighFrequencyTimerCounts;
const int THREAD_START_DELAY_MS = 650;
/* USER CODE END PV */

void SystemClock_Config(void);
void MX_FREERTOS_Init(void);
/**
  * @brief  The application entry point.
  * @retval int
  */
int main(void)
{

  /* MCU Configuration--------------------------------------------------------*/

  /* Reset of all peripherals, Initializes the Flash interface and the Systick. */
  HAL_Init();

  /* Configure the system clock */
  SystemClock_Config();

  /* Initialize all configured peripherals */
  MX_GPIO_Init();
  MX_DMA_Init();
  MX_FDCAN1_Init();
  MX_FDCAN2_Init();
  MX_I2C2_Init();
  MX_SPI1_Init();
  MX_USART2_UART_Init();
  MX_TIM16_Init();
  MX_CRC_Init();
  /* USER CODE BEGIN 2 */
  MX_USB_Device_Init();

  /* USER CODE END 2 */

  /* Init scheduler */
  osKernelInitialize();

  /* Call init function for freertos objects (in cmsis_os2.c) */
  MX_FREERTOS_Init();

  /* Start scheduler */
  osKernelStart();

  /* We should never get here as control is now taken by the scheduler */

  /* Infinite loop */
  /* USER CODE BEGIN WHILE */
  while (1)
  {
    /* USER CODE END WHILE */

    /* USER CODE BEGIN 3 */
  }
  /* USER CODE END 3 */
}

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
/* USER CODE BEGIN 4 */

void configureTimerForRunTimeStats(void)
{
    ulHighFrequencyTimerCounts = 0;
    HAL_TIM_Base_Start_IT(&htim16);
}

unsigned long getRunTimeCounterValue(void)
{
	return ulHighFrequencyTimerCounts;
}

/* USER CODE END 4 */

/**
  * @brief  Period elapsed callback in non blocking mode
  * @note   This function is called  when TIM6 interrupt took place, inside
  * HAL_TIM_IRQHandler(). It makes a direct call to HAL_IncTick() to increment
  * a global variable "uwTick" used as application time base.
  * @param  htim : TIM handle
  * @retval None
  */
void HAL_TIM_PeriodElapsedCallback(TIM_HandleTypeDef *htim)
{
  if (htim->Instance == TIM6) {
    HAL_IncTick();
  }
}

/**
  * @brief  This function is executed in case of error occurrence.
  * @retval None
  */
void Error_Handler(void)
{
  /* USER CODE BEGIN Error_Handler_Debug */
  /* User can add his own implementation to report the HAL error return state */
  __disable_irq();
  while (1)
  {
  }
  /* USER CODE END Error_Handler_Debug */
}

#ifdef  USE_FULL_ASSERT
/**
  * @brief  Reports the name of the source file and the source line number
  *         where the assert_param error has occurred.
  * @param  file: pointer to the source file name
  * @param  line: assert_param error line source number
  * @retval None
  */
void assert_failed(uint8_t *file, uint32_t line)
{
  /* USER CODE BEGIN 6 */
  /* User can add his own implementation to report the file name and line number,
     ex: printf("Wrong parameters value: file %s on line %d\r\n", file, line) */
  /* USER CODE END 6 */
}
#endif /* USE_FULL_ASSERT */

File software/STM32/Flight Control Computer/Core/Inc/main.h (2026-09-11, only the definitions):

#define GPIO2_Pin GPIO_PIN_13
#define GPIO2_GPIO_Port GPIOC
#define FLOW_CS_Pin GPIO_PIN_14
#define FLOW_CS_GPIO_Port GPIOC
#define ACCEL_INT_Pin GPIO_PIN_15
#define ACCEL_INT_GPIO_Port GPIOC
#define ACCEL_INT_EXTI_IRQn EXTI15_10_IRQn
#define GYRO_CS_Pin GPIO_PIN_0
#define GYRO_CS_GPIO_Port GPIOA
#define GYRO_INT_Pin GPIO_PIN_1
#define GYRO_INT_GPIO_Port GPIOA
#define GYRO_INT_EXTI_IRQn EXTI1_IRQn
#define ACCEL_CS_Pin GPIO_PIN_4
#define ACCEL_CS_GPIO_Port GPIOA
#define CC2500_GDO0_Pin GPIO_PIN_0
#define CC2500_GDO0_GPIO_Port GPIOB
#define CC2500_CS_Pin GPIO_PIN_1
#define CC2500_CS_GPIO_Port GPIOB
#define CC2500_GDO2_Pin GPIO_PIN_2
#define CC2500_GDO2_GPIO_Port GPIOB
#define CC2500_GDO2_EXTI_IRQn EXTI2_IRQn
#define GPIO8_Pin GPIO_PIN_10
#define GPIO8_GPIO_Port GPIOB
#define GPIO9_Pin GPIO_PIN_11
#define GPIO9_GPIO_Port GPIOB
#define MAG_DRDY_Pin GPIO_PIN_12
#define MAG_DRDY_GPIO_Port GPIOB
#define MAG_DRDY_EXTI_IRQn EXTI15_10_IRQn
#define MAG_INT_Pin GPIO_PIN_13
#define MAG_INT_GPIO_Port GPIOB
#define BMP_INT_Pin GPIO_PIN_14
#define BMP_INT_GPIO_Port GPIOB
#define BMP_INT_EXTI_IRQn EXTI15_10_IRQn
#define GPIO7_Pin GPIO_PIN_15
#define GPIO7_GPIO_Port GPIOB
#define GPIO6_Pin GPIO_PIN_10
#define GPIO6_GPIO_Port GPIOA
#define GPIO5_Pin GPIO_PIN_15
#define GPIO5_GPIO_Port GPIOA
#define GPIO4_Pin GPIO_PIN_4
#define GPIO4_GPIO_Port GPIOB
#define GPIO1_Pin GPIO_PIN_7
#define GPIO1_GPIO_Port GPIOB

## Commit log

2024-09-13 init hardware and software folders. import current work
    [CC2500EM_PARTLIST_3_0.xls, ESC_KiCAD.kicad_pcb, ESC_KiCAD.kicad_sch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]
2024-09-14 update software mcu esc
2024-10-22 esc sensing circuitry
    [ESC_KiCAD.kicad_sch, mcu.kicad_sch, phases.kicad_sch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]
2024-10-22 update FCC stm32 ioc file
    [phases.kicad_sch]
2024-10-23 update FCC bom
    [bom.csv]
2024-10-23 add revision to FCC pdf, fix mcu boot option bytes, blink an LED!
    [FCC_KiCAD.kicad_sch, I2C.kicad_sch, MCU.kicad_sch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]
2024-10-27 starting bmi driver...
2024-11-02 add GCS v1 and bmi088 driver
2024-12-03 add BMP388 press sensor driver, GCS rework to PyQT6
    [Flight Control Computer.ioc, app_freertos.c, main.h]
2024-12-15 add lis3mdl magnetometer driver
2024-12-15 update stm32 cubeide
2024-12-16 add hard iron calibration to magnetometer
2025-02-01 change drivers to C++, add software IIR filtering, improve GCS software
    [ESC_KiCAD.kicad_sch, pwr_usb_can.kicad_sch]
2025-02-01 improve IIR filter to second order Butterworth low pass
2025-02-17 adjust filter cutoff
2025-03-08 separation of logging into indep. thread, use threads flags, general refactor and optimization
2025-05-24 sensor fusion v1 !!!
2025-05-25 add barometer filtering and complimentary filter validity check
2025-12-23 finish ESC hardware RevA, CC2500 driver working
    [ESC_BOM.csv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]
2025-12-26 driver tuning
2025-12-27 sensor fusion tuning
2025-12-28 add leaky integrator to sensor fusion algorithm

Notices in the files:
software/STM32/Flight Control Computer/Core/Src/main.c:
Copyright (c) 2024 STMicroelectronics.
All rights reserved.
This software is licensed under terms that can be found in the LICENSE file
